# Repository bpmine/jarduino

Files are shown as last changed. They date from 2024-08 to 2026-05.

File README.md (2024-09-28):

# Jarduino

Le Jarduino est un ensemble de systèmes pour l'arrosage du jardin.

Il comporte les sous-ensembles suivants:
- Gestion des goutteurs
- Gestion des cuves
- Gestion des oyas

Le principal objectif du projet est de s'amuser tout en mettant à profit les compétences acquises lors d'une réponse à un cahier des charges pour un projet professionnel qui n'a finalement pas abouti.

La réalisation inclue des cartes électroniques conçues sur mesure, du logiciel, quelques petites pièces mécaniques et bien d'autres éléments....

## Illustrations (photos)

## Gestion des goutteurs

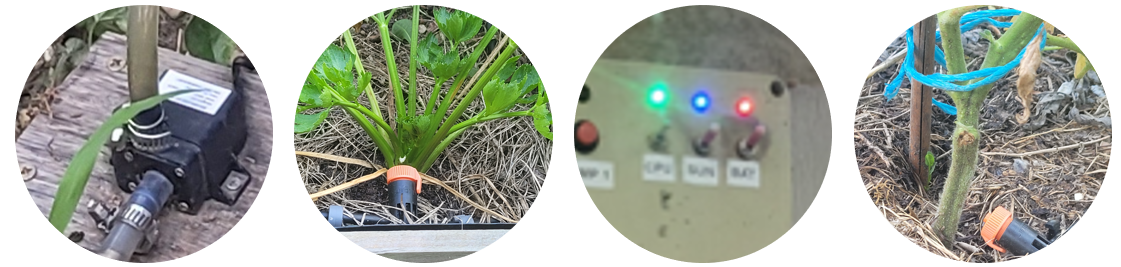
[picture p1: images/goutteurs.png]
Goutteurs


### Aux origines...

Le système de goutteurs est le "Jarduino" historique, mis en place assez rapidement (en 2019 ?) pour partir en vacances sans s'occuper de l'arrosage.

Il a fonctionné presque jusqu'au bout. Le panneau solaire s'est retourné (vent?), et sans énergie, il s'est arrêté...

Depuis 2019, chaque année, le Jarduino fonctionne toujours en se perfectionnant. Il a compté jusqu'à une cinquantaine de goutteurs en 2022.

### Jarduino 2

Ce Jarduino est un peu plus sérieux, basé sur de vraies cartes électroniques et non plus sur des platines de prototypage.

Il a été prévu en deux étapes:
- Tout d'abord une version simple basée sur un arduino Nano et une RTC;
- ensuite, une connexion Wifi via un ESP01 et la liaison série / modbus.

Il a fonctionné sans difficultés. Mais le module Wifi n'est toujours pas prêt (en 2024)...

#### Principe

Une cuve permet de stoker de l'eau. Un boîtier de contrôle alimenté par un panneau solaire avec une batterie pilote une pompe qui allimente les goutteurs.
Le boîtier pilote jusqu'à deux pompes et peut être programmé à une heure donnée pour une durée d'arrosage souhaitée.

Voir ici la description détaillée: [Système de goutteurs](./goutteurs)

## Gestion des cuves

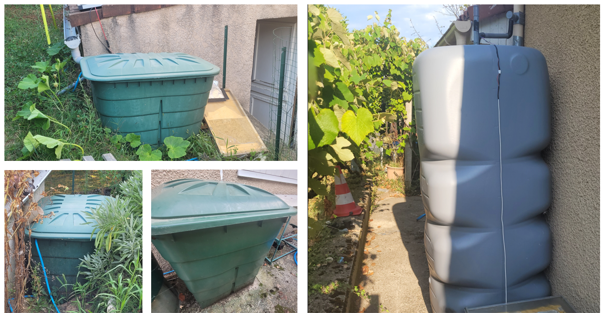
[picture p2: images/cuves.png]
Cuves


Plusieurs cuves récupèrent l'eau de pluie et permettent d'approvisioner les systèmes d'arrosage automatiques.
Un système de pompes contrôlables à distance permet de gérer leur niveau.

Voir ici la description détaillée: [Gestion des cuves](./cuves)

## Gestion des OYAs

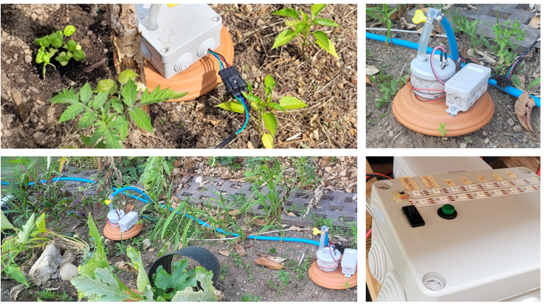
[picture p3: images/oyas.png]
Oyas


Le système permet de diffuser de l'eau aux plantes par la terre grâce à des sortes de petites jarres en argile appellées OYAs.
Ce dispositif a été déployé après les goutteurs, en 2023. Il remplace petit à petit le système de goutteurs.

Voir ici la description détaillée: [Gestion des OYAs](./oyas)

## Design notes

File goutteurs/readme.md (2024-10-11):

# Goutteurs (Jarduino2)

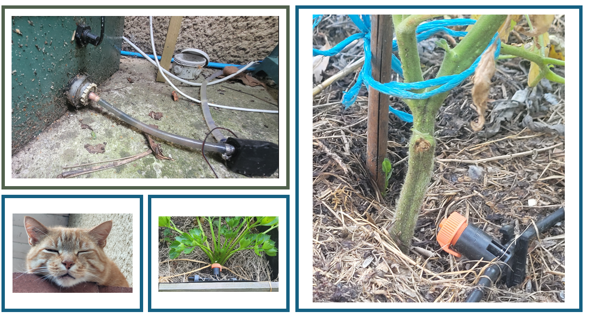
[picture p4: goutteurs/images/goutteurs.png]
Goutteurs


Jarduino2 est une évolution du premier jarduino fabriqué en 2019.

Le premier jarduino était construit avec des platines de prototypage et un arduino MKR Zero Wifi.

Ce nouveau jarduino est construit à partir d'un Nano. On peut le configurer à l'aide d'une interface MODBUS sur l'USB ou bien sur le port série d'extension.
Il est possible de lui ajouter une extension Wifi pour le relier au réseau.

## Vue d'ensemble

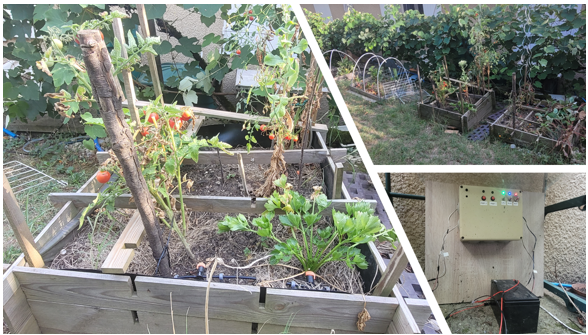
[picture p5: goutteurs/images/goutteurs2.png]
Goutteurs


Deux systèmes jarduinos étaient actifs en 2024, couvrant deux zones de jardin.
Chaque système est alimenté par une cuve à l'aide d'une pompe ou deux pompes.

Un coffret de commande permet de mettre ou non en service le système et de déclencher un arrosage en mode manuel.

Chaque coffret peut se programmer à l'aide d'un logiciel PC connecté à l'USB de la carte de commande. Cela permet d'activer ou non le mode automatique et de choisir l'heure de déclenchement et la durée d'arrosage.

Le coffret dispose de deux sorties pouvant commander deux pompes. Chaque voie peut alimenter jusqu'à 20 goutteurs. 

## Hardware

### Caractéristiques

  - Alimentation 12V;
  - Entrée de mesure de tension de panneau solaire;
  - 2 sorties 5W pour pompe (De type aquarium);
  - Sonde de température/Humidité;
  - LEDs et interrupteurs.

### Schéma

[Schéma de la carte de commande](./hard/jarduino2_nano/jarduino2_nano.pdf)

[Schéma de la carte d'interface à LEDs](./hard/jarduino2_ihm/jarduino2_ihm.pdf)

### PCBs

Chaque boîtier/coffret de commande est composé de deux circuits imprimés (PCBs):
- La carte de commande contient le microcontrôleur et gère tout le système
- la carte d'interface permet à l'utilisateur visualiser le fonctionnement et d'agir sur celui-ci.

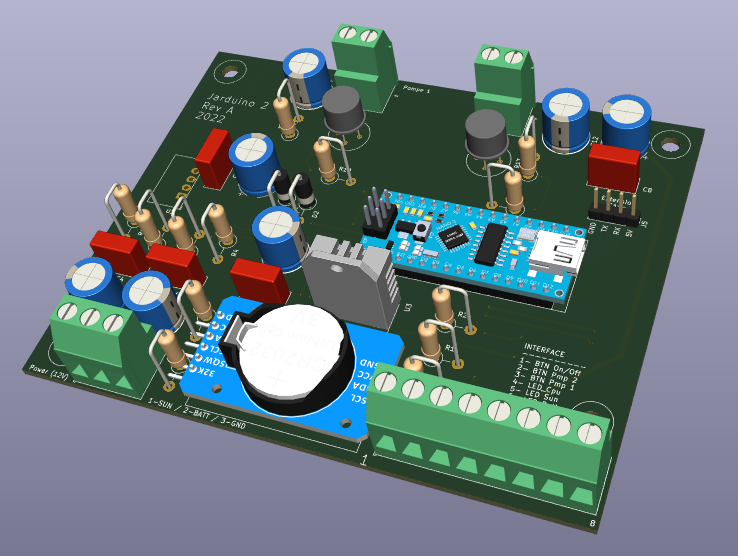
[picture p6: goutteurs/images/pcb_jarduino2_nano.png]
Carte de commande Jarduino2 Nano


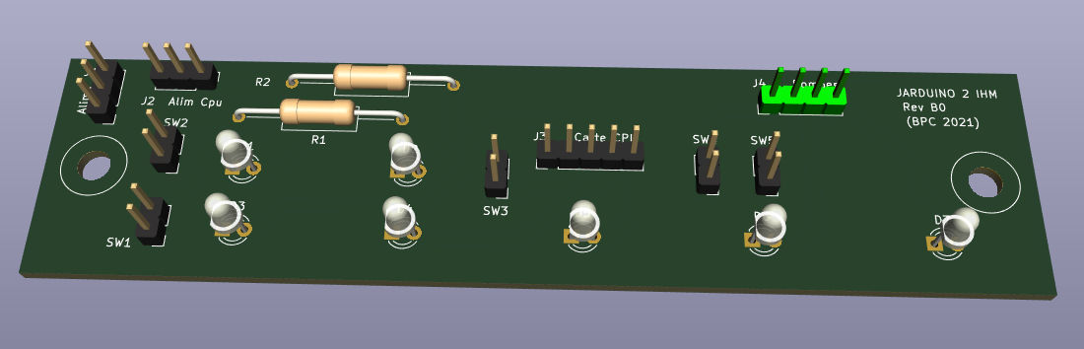
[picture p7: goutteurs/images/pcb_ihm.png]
Carte d'interface à LEDs


### Boîtier de commande

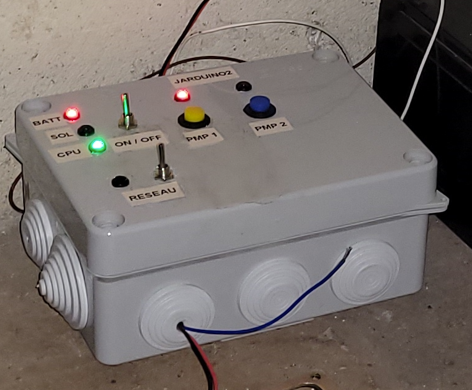
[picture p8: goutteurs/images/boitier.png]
Boîtier de commande Jarduino2


| LED | Description |
| --- | --- |
| BATT | Batterie OK |
| SUN | Panneau photovoltaique OK |
| Réseau | Réseau Wifi Activé |

NB: Il n'y a pas à ce jour (en 2024) de module Wifi terminé et apte à se connecter au réseau de domotique de la maison. C'est une fonction prévue à l'origine mais qui ne verra peut-être pas le jour puisque nous sommes en train de remplacer les goutteurs par des OYAs.

| Bouton | Type | Description |
| --- | --- | --- |
| ON/OFF | Inverseur  | Bouton de mise en service (Ne coupe pas l'alimentation mais fait passer le CPU en veille) |
| Réseau | Inverseur  | Bouton de mise sous tension de la carte Wifi (si présente) |
| Pump 1 | Poussoir  | Bouton de démarrage de l'arrosage manuel de la voie 1 |
| Pump 2 | Poussoir  | Bouton de démarrage de l'arrosage manuel de la voie 2 |

Le boîtier comporte les entrées/sorties suivantes:

| Voie | Type | Description |
| --- | --- | --- |
| Alimentation | Alim 12V  | Connexion d'une batterie extérieure (Plomb) |
| solaire | Alim 12V/20V | Connexion d'un panneau solaire pour recharger la batterie |
| Pompe 1 | Sortie 12V | Sortie de commande de la pompe 1 |
| Pompe 2 | Sortie 12V | Sortie de commande de la pompe 2 |

NB: Un module chargeur/régulateur solaire se trouve dans le boîtier pour permettre la charge de la batterie à l'aide du panneau solaire relié.

Ce système s'est avéré suffisant pour gérer le décalage entre les horaires à forte énergie solaire (jour) et la plage horaire idéale pour arroser (soirée/début de nuit).

## Logiciels

### Logiciel embarqué dans la carte de commande

[Logiciel gestion des goutteurs](./src)

### Logiciel PC pour configurer le système

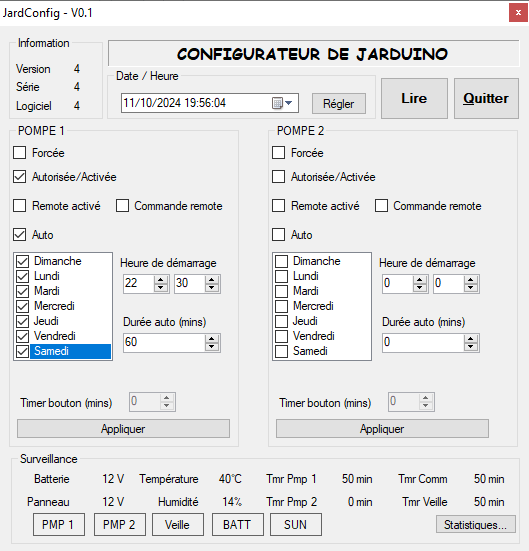
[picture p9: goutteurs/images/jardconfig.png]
Le logiciel JardConfig


Ce logiciel permet de configurer le boîtier Jarduino.
Pour cela, on branche un PC à l'USB de la carte de commande.

On peut:
- Régler l'heure

Et pour chaque voie (1 ou 2):
- Forcer la commande de la pompe
- Activer ou désactiver la pompe
- Activer et simuler le pilotage distant de la pompe
- Sélectionner le mode Auto (basé sur l'horloge)
- Régler l'heure d'arosage automatique
- Régler la durée de l'arrosage automatique
- Sélectionner les jours de semaine de l'arrosage automatique

Il permet également d'afficher l'état du système et quelques statistiques de fonctionnement.

Le logiciel communique avec le boîtier Jarduino à l'aide du protocole MODBUS (Voir ci-après).

## Protocole MODBUS

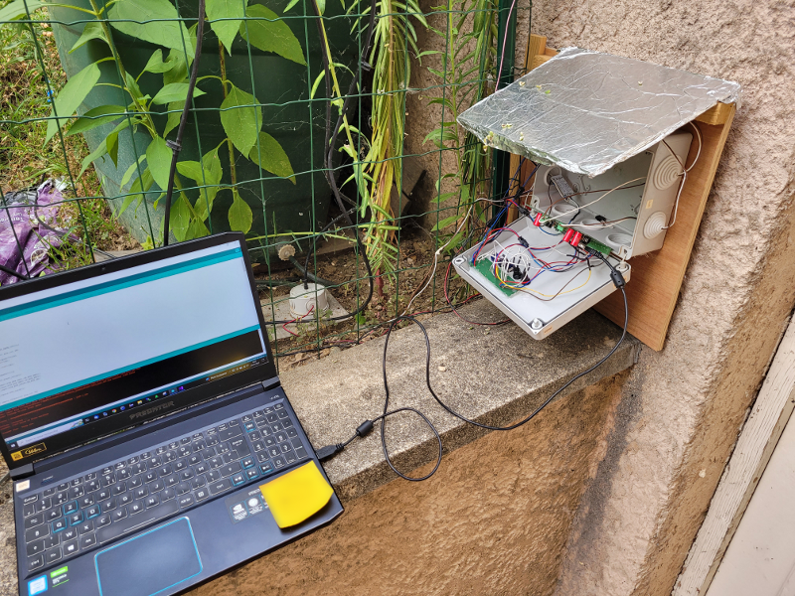
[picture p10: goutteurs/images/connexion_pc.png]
Connexion au PC


Le jarduino implémente un serveur/esclave MODBUS.

Seules les functions suivantes sont implémentées:

- 01 READ COIL STATUS
- 02 READ INPUT STATUS
- 03 READ HOLDING REGISTERS
- 04 READ INPUT REGISTERS
- 15 WRITE MULTIPLE COILS
- 16 WRITE MULTIPLE REGISTERS

### Table des COILs (Lecture/Ecriture)

Adresse | Description
--- | ---
10 | Forçage POMPE 1
11 | Autorisation/Activation POMPE 1
12 | Mode automatique POMPE 1
13 | Mode Distant POMPE 1
14 | Commande distante POMPE 1
--- | ---
20 | Forçage POMPE 2
21 | Autorisation/Activation POMPE 2
22 | Mode automatique POMPE 2
23 | Mode Distant POMPE 2
24 | Commande distante POMPE 2

Ces bits sont enregistrés en EEPROM sauf ceux qui correspondent au forçage des pompes et à leur commande distante.

NB: La commande à distance des pompe est appliquée seulement si le maître modbus communique toujours avec le jarduino nano.

### Table des Entrees (Lecture)

Adresse | Description
--- | ---
0 | Etat LED pompe 1
1 | Etat LED pompe 2
2 | Tension battery OK
3 | Tension panneau solaire OK
4 | Est en mode veille

### Table des INPUT REGISTERs (Lecture)

Adresse | Description
--- | ---
0 | Niveau de batterie en dxV
1 | Niveau du panneau solaire en dxV
2 | Temperature en °C
3 | Humidité en %
4 | Temps restant avant détection Comm perdue (en ms)
5 | Temps restant avant veille (en ms)
--- | ---
10 | Temps restant timer de pompe 1 (en min)
--- | ---
20 | Temps restant timer de pompe 2 (en min)
--- | ---
100 | Nombre total de boots
101 | Temps de fonctionnement total POMPE 1 (en H)
102 | Temps de fonctionnement total POMPE 1 (en H)
103 | Temps total d'ensoleillement (en H)
104 | Nombre total de pressions sur le bouton POMPE 1
104 | Nombre total de pressions sur le bouton POMPE 2
--- | ---
200 | Version (2 pour jarduino 2)
201 | Numéro de série du Jarduino
202 | Version du logiciel nano

### Table des HOLDING REGISTERs (Lecture/Ecriture)

Adresse | Description
--- | ---
0 | Année
1 | Mois
2 | Jour
3 | Heure
4 | Minute
5 | Seconde
--- | ---
10 | Heure de démarrage POMPE 1
11 | Minute de démarrage POMPE 1
12 | Durée (en min) d'activation de la POMPE 1
13 | Jours de la semaine pour l'activation de la POMPE 1 (Bit 0: Dimanche, Bit 1: Lundi, ..., Bit 7: Samedi)
14 | Réglage du délai du timer de pompe 1 (en min)
--- | ---
20 | Heure de démarrage POMPE 2
21 | Minute de démarrage POMPE 2
22 | Durée (en min) d'activation de la POMPE 2
23 | Jours de la semaine pour l'activation de la POMPE 2 (Bit 0: Dimanche, Bit 1: Lundi, ..., Bit 7: Samedi)
24 | Réglage du délai du timer de pompe 2 (en min)

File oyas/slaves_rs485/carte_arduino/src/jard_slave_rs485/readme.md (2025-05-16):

# Logiciel Esclave RS485 Oyas/Pompe

Ce logiciel pilote un noeud RS485 du système Oyas.
Logiciel compatible avec un module Arduino Nano.

## Protocole

Voir ../../../readme.md

## Taille du programme

| Description | Taille |
| --- | --- |
| Mémoire Flash | 11,154 kOctets |
| RAM | 485 Octets|

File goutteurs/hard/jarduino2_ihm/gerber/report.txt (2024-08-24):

Plot file "C:\DEV\GITHUB\modules_uino\jarduino2\schema\jarduino2\jarduino2_ihm\gerber\jarduino2_ihm-B_Cu.gbr" created.
Plot file "C:\DEV\GITHUB\modules_uino\jarduino2\schema\jarduino2\jarduino2_ihm\gerber\jarduino2_ihm-F_SilkS.gbr" created.
Plot file "C:\DEV\GITHUB\modules_uino\jarduino2\schema\jarduino2\jarduino2_ihm\gerber\jarduino2_ihm-B_Mask.gbr" created.
Plot file "C:\DEV\GITHUB\modules_uino\jarduino2\schema\jarduino2\jarduino2_ihm\gerber\jarduino2_ihm-Edge_Cuts.gbr" created.
Créer le fichier Gerber "job"  "C:\DEV\GITHUB\modules_uino\jarduino2\schema\jarduino2\jarduino2_ihm\gerber\jarduino2_ihm-job.gbrjob"

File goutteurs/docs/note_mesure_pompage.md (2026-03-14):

# Pompe jarduino historique (AD20P-1230A)

## Caractéristiques

| Caractéristique | Valeur |
|--|--|
| Tension | 12V cc |
| Courant | 400 mA |
| Puissance | 4.2 W |
| Débit maximum | 240 L/H |
| Hauteur maximum | 3 m |
| Pression | ? |
| Embouts | 8mm |

## Mesures

### Mesure jardin Paul (tuyau arrivee)

1L rempli en 02 mins 56 secs
20,5 L/H

~12 V

Environ 1m de dénivelé

### Mesure jardin côté réduit à bois (tuyau arrivee)

1L rempli en 7 mins 59 secs
8,57 L/H

Environ 1m50 de dénivelé

# Pompe AW500S

## Caractéristiques

| Caractéristique | Valeur |
|--|--|
| Tension | 12V cc |
| Courant | 920 mA |
| Puissance | 19 W |
| Débit maximum | 800 L/H |
| Hauteur maximum | 5 m |
| Pression | ? |
| Embouts | 20mm Vis mâle |

# Mesure 1
1L rempli en 14s
257L/H

12,7V
1,23A
15,5W

Conditions: Environ 1,5m de dénivelé

# Mesure 2
1,5L rempli en 37s
146L/Heure

Conditions: De la cuve principale vers celle du réduit via Wifi IO (et via EV ON)

# Pompe DP521

## Caractéristiques

Pompe à eau à membrane

| Caractéristique | Valeur |
|--|--|
| Tension | 12V cc |
| Courant | 2 A |
| Débit maximum | 3.5 L/H |
| Pression | 0.48 MPa |
| Embouts | 10 mm |

## Mesure de débit

Direct sur lavabo mais en passant par une EV

1,5 L rempli en 30S
Soit  3L/min (180 L/H)

A noter que la pompe fuit au niveau de ses vis si on bloque la sortie.

## Mesures électriques

Dispositif avec bidon lave glace modifié -> Filtre -> Pompe -> Débimètre -> EV

| Grandeur | Condition | Valeur |
| --- | --- | --- |
| Tension à la pompe | Avec de l'eau | 12,02 V |
| Courant dans la pompe | Avec de l'eau | 1,15 A |
| Puissance pompe | Avec de l'eau | 13,9 W |
| Tension à la pompe | Sans eau | 12,02 V |
| Courant dans la pompe | Sans eau | 0,66 A |
| Puissance pompe | Sans eau | 7,9 W |

Note: Le wattmètre consomme environ 1,24 W

Mesures complémentaires sur l'électrovanne:

| Grandeur | Condition | Valeur |
| --- | --- | --- |
| Tension EV | Pompe OFF | 12,20 V |
| Courant EV | Pompe OFF | 0,59 A |
| Puissance EV| Pompe OFF | 7 W |
| Tension EV | Pompe ON | 12,02 V |
| Courant EV | Pompe ON | 0,56 A |
| Puissance EV| Pompe ON | 6,7 W |

Note: Le wattmètre consomme environ 1,24 W

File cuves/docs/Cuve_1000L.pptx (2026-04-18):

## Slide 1

Mât avec capteurs de niveaux pour cuve 1000 L

2m

180cm
(Haut
cuve)

- Perçage
- Découpe à l'arrière pour visser le capteur
- Soudure arrière
- Eventuellement résine

140cm (Max)

90cm (Milieu)

Hauteur | Volume (L) | Volume (m³)
180 cm | 1000 | 1
140 cm | 778 | 0,778
90 cm | 500 | 0,500
20 cm | 111 | 0,111

20cm (Mini)

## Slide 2

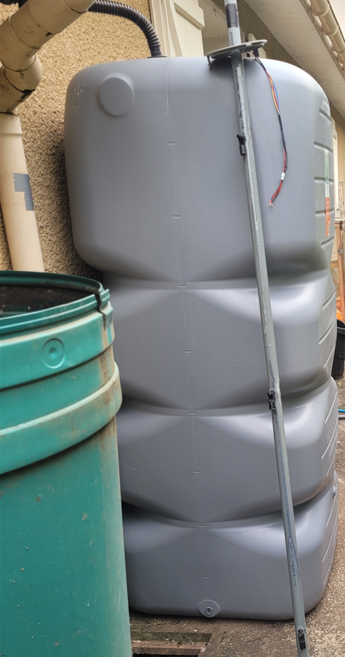
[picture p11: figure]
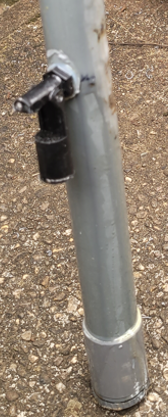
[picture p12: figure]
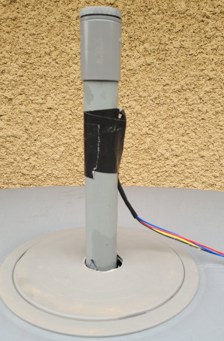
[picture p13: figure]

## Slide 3

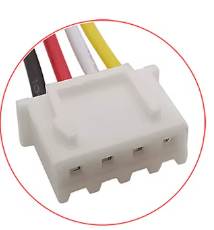
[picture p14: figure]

Bas

Milieu

Haut

Commun

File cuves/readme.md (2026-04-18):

# Cuves

Nous avons 4 cuves pour une capacité totale de 2200 L.

- Cuve principale de 1000 L
- cuve  "Paul" de 300 L
- cuve "Réduit" de 520 L
- cuve "Barbec" de 520 L

Deux cuves de 520 L et une de 300 L alimentent nos deux systèmes de remplissage automatique des OYAs.

Les cuves sont communicantes et un système permet de pomper l'eau de la cuve principale vers les autres. 

## Description des cuves

### Cuve principale (Main)

Cette cuve recueille l'eau du toit de la maison. D'une capacité de 1000 L, elle constitue la réserve principale.
Elle sert à alimenter la cuve "Paul" et aussi la cuve "Réduit" en cas de besoin.

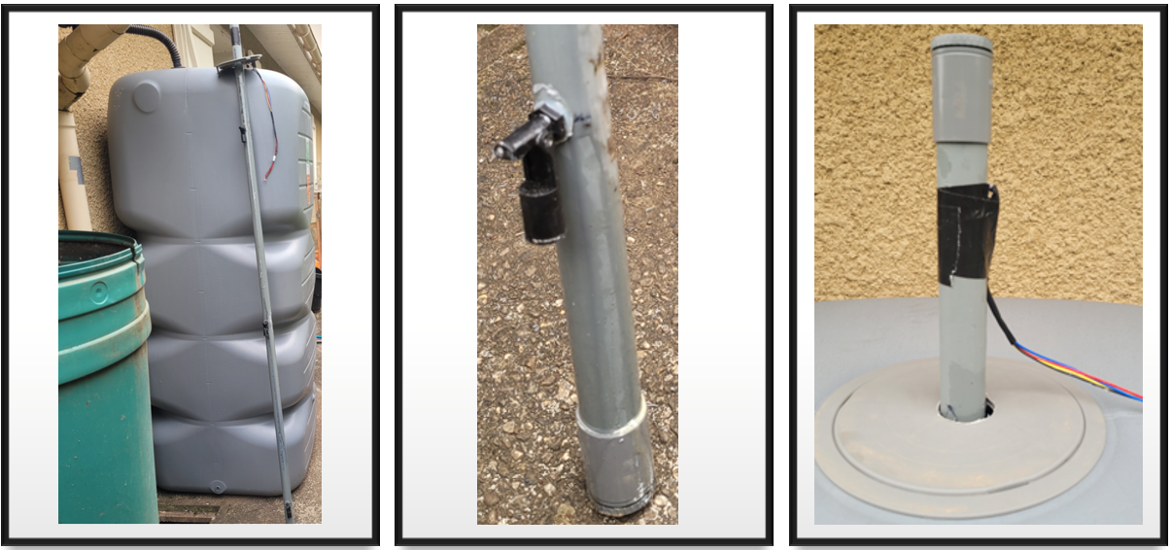
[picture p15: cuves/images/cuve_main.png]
Cuve principale 1000L


Comme on peut le voir sur la troisième photo, une colonne PVC de 32mm est utilisée comme jauge de niveau.
Cette solution permet d'éviter de percer des trous dans la paroi de la cuve (comme pour les autres).

Trois capteurs à flotteur sont fixés sur cette colonne qui ensuite est remplie de résine pour rendre le tout étanche et durable:

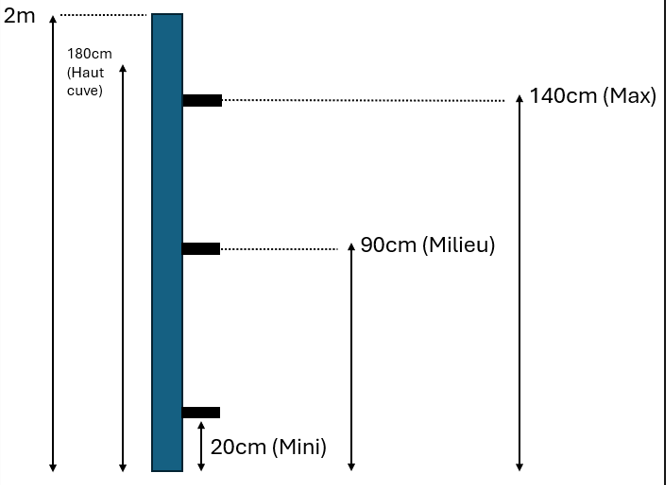
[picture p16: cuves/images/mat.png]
Mât de mesure


A la base de la cuve, un système de 2 pompes (précédées de filtres) permet de déplacer l'eau vers les autres cuves (Paul et Réduit):

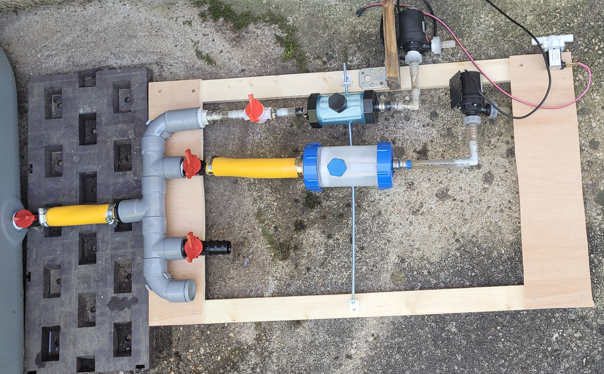
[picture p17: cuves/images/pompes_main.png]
Système de pompes


Le modèle de pompe utilisé est le AW500S 12V 5m 800L/H:

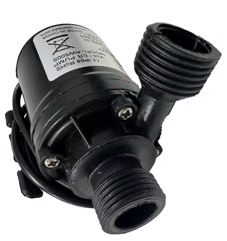
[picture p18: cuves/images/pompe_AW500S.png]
Pompe AW500S 12V 5m 800L/H


Pour la petite histoire, nous disposions avant 2023 à cet emplacement d'une cuve de moindre contenance.
Mal positionnée sur son support, un jour de pluie elle est tombée de tout son poids et BOOM !

Depuis, elle marche moins bien...

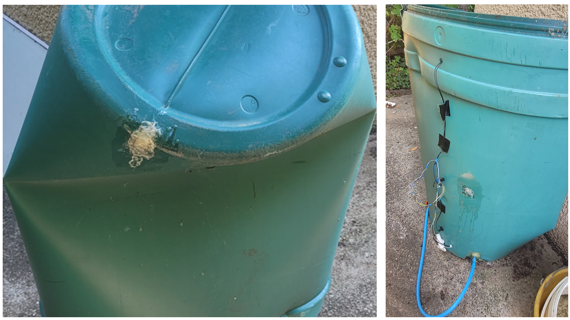
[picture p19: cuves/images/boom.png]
Cuve cassée


### Cuve Paul

La cuve "Paul" (de Paul) de 220 L permet d'alimenter un système de 6 oyas (en 2025). Anciennement, elle alimentait les derniers goutteurs pour des bacs de jardinage (5 bacs en 2024).

La détection de niveau est réalisée à l'aide de 3 capteurs avec flotteur montés sur la paroi de la cuve.

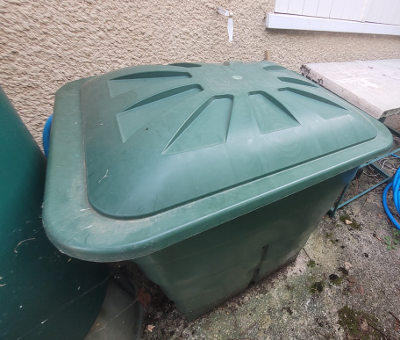
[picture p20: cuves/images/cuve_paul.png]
Cuve Réduit


### Cuve Réduit

Cette cuve de 520 L alimente un système de remplisage d'OYAs et permet également d'alimenter la cuve Barbecue si besoin.

La détection de niveau est réalisée à l'aide de 3 capteurs avec flotteur montés sur la paroi de la cuve. 

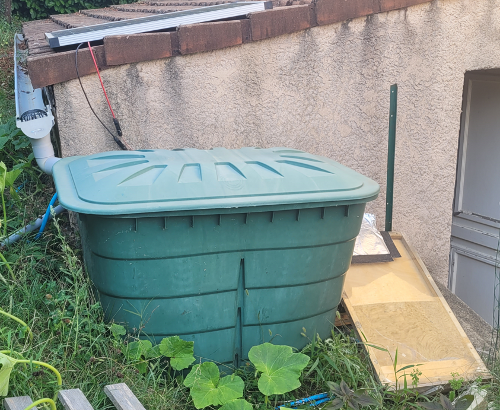
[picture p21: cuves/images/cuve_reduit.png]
Cuve Réduit


Le système de capteurs a montré ses limites car des fuites sont apparus au bout d'un an d'utilisation au niveau de ces capteurs.
Pour pallier au problème, de la résine a été utilisée pour recouvrir la zone sensible autour des capteurs.

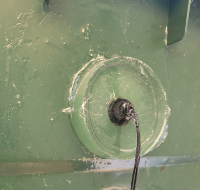
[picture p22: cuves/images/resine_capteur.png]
Résine sur les capteurs


### Cuve Barbecue

Cette cuve de 520 L alimente un système de remplisage d'OYAs et un système de goutteurs.
La détection de niveau est réalisée à l'aide de 3 capteurs avec flotteur montés sur la paroi de la cuve. 

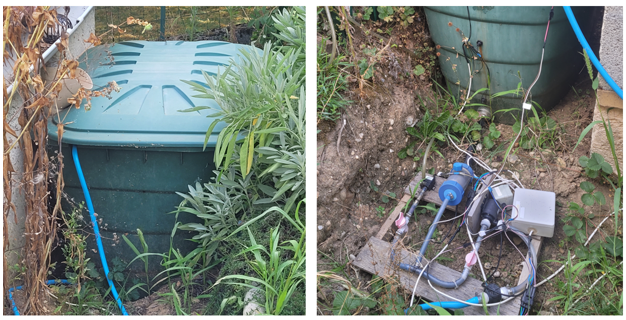
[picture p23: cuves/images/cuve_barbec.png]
Cuve Barbecue


## Filtres imprimés en 3D

Les électrovannes utilisées pour les OYAs et le transfert de l'eau inter-cuves, les pompes et les goutteurs requièrent une eau parfaitement filtrée.
Si pour les goutteurs d'entrée 8mm, cela paraît évident, il faut savoir que c'est également nécessaire pour les électrovannes. En effet, de petits morceaux d'algues peuvent bloquer une électrovanne en position ouverte.

C'est la raison pour laquelle des filtres ont été ajoutés à plusieurs endroits sur le tuyau (Cuves Paul, Réduit et Barbecue).

### Filtre sortie vers tuyau 4mm/8mm

Une pièce a été conçue et imprimée pour filtrer directement sur le tuyau PVC de sortie des cuves.
Elle a été utilisée avant 2023 lorsque tous les systèmes d'arrosages étaient en version goutteurs.

Ce filtre permet de brancher un tuyau 4 mm vers le système de gouteurs. 
Trop fragile, une version similaire avec une sortie 8 mm a ensuite été imprimée.

### Pré-filtre intérieur

Pour filtrer de plus gros morceaux avant le tuyau de sortie, la pièce suivante est vissée à l'intérieur des cuves (Réduit et Barbecue).

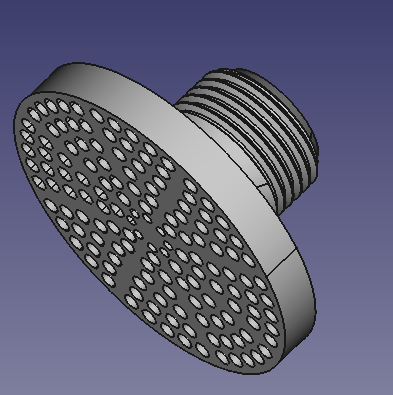
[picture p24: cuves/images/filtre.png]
Filtre intérieur


## Modules Wifi pour commander les pompes

### Description

Le module de pompage comporte:
- 1 alimentation 12V;
- 1 sortie pompe de 12V/5A;
- 3 entrées de type interrupteur (actif à l'état bas) pour la détection du niveau de cuve.

### Carte Wifi IO

Deux versions de cartes ont été réalisées:
- Carte wemos
- carte C3

La première à base d'un Wemos D1 mini (ESP8266). Cette carte fonctionne depuis 2024. Son boitier est petit et cela pose un problème avec la condensation. En 2025, deux cartes étaient déjà oxydées car elles baignaient dans l'eau. les boitiers ne sont pas parfaitement étanches.
Le projet se trouve ici: [Carte wemos](./carte_wemos)

La carte C3 est basée sur un module ESP32 C3 mini. Elle est censée mieux fonctionner... Fabriquée en 2026, elle est placée dans une boîte de dérivation plus grosse pour éviter que la condensation atteigne la carte.
Le projet se trouve ici: [Carte C3](./carte_c3)

La carte wemos s'avère plus puissante niveau Wifi et porte un peu plus loin. Les cartes C3 un peu moins bonnes et dépendantes de leur module C3 (dispertion).
Malgré tout, les cartes C3 semblent fonctionner correctement.

### Protocole d'échange avec MQTT

## Serveur de contrôle

Le serveur comporte un broker MQTT pour centraliser les connexions des différents modules du système.

Un serveur reddis stocke tous les états, les réglages et les commandes des différentes applications.

Les applications sont les suivantes:
- Interraction avec les modules de pompage
- Publication des états sur les écrans
- Webservice pour exposer les services à des clients
- Automatisme de contrôle
- Logger

## Module d'affichage

Le module d'affichage comporte un écran, OLED.

Il permet de visualiser l'état des cuves et l'activité de pompage en temps réel.

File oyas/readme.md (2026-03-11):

# Système de gestion des OYAs

## Présentation

Le but du système de remplissage automatique des OYAs est de pouvoir s'absenter pendant les vacances tout en laissant les OYAs se gérer tous seuls.

### Oyas

Les OYAs sont des sortes de pots en argile enterrés utilisés depuis des millénaires pour distribuer de l'eau à des cultures.

On remplit régulièrement ces pots. Grâce à leur porosité, l'eau se diffuse à travers l'OYAs au fur et à mesure où les racines des plantes assèchent la terre à proximité.

- Ils évitent les pertes d'eau par évaporation
- ne mouillent pas les feuilles des plantes
- ne mouille pas le sol en surface
- évitent le stress hydrique
- permettent de faire des économies d'eau

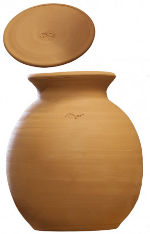
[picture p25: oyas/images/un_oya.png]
Un OYA


### Principe de fonctionnement

Des cuves récupèrent l'eau de pluie. A partir de ces cuves, un système comportant une pompe et plusieurs électrovannes permet de remplir les OYAs.

Le système rempli chaque OYA jusqu'au maximum ou bien selon le programme souhaité. La stratégie de remplissage est entièrement programmable.

## Description de nos réseaux d'OYAs

Notre installation comporte actuellement (en 2025) trois réseaux d'OYAs reliés chacun à une cuve et à son alimentation électrique autonome.

## Réseau A : Barbecue

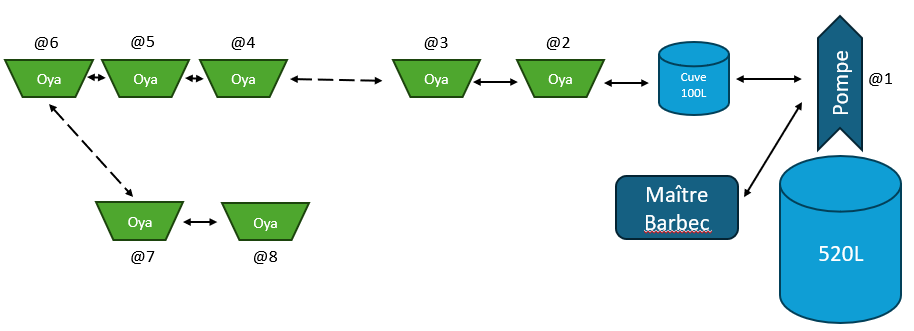
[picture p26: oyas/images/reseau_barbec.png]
Réseau Barbecue


C'est le plus ancien (mise en service en 2023). Il comporte à ce jour:

- 1 maître
- 1 pompe
- 7 OYAs
- 1 EV pour remplir un réservoir d'appoint

 Caractéristique | Description
-- | --
Nombre de nœuds | 10
Longueur | environ 30 m
Volume cuve | 520 L
Capacité totale des Oyas | 64 L (4x10 + 3x8 + cuve de 100L non gérée actuellement)
Alimentation | 1 Panneau solaire 120W + 2 Batteries 12V au plomb

La cuve et l'alimentation 12V déservent à la fois le système d'OYAs et un système de gestion de goutteurs alimenté par une petite pompe.

Ce réseau est à la fois composé de cartes électroniques  esclaves de "première génération" Rev Ax et de cartes récentes (Rev Gx produites en 2024).

Très bon retour sur le fonctionnement pendant l'été 2023. 
Excellent retour aussi en 2024.

A noter cependant la fragilité des électrovannes. Pour fonctionner correctement, il est nécessaire d'avoir une eau d'arrivée sans impureté. En effet, celle ci peut se déposer entre le corps et la membrane de l'électrovanne et bloquer cette dernière en position ouverte. Le tuyau 10mm transparent génère des algues qui sèchent pendant l'hiver lors de l'entreposage du système. Lors de la remise en service au printemps 2023, des morceaux d'algue de l'année précédente se sont détachées et sont venues perturber le fonctionnement des électrovannes.

## Réseau B : Réduit

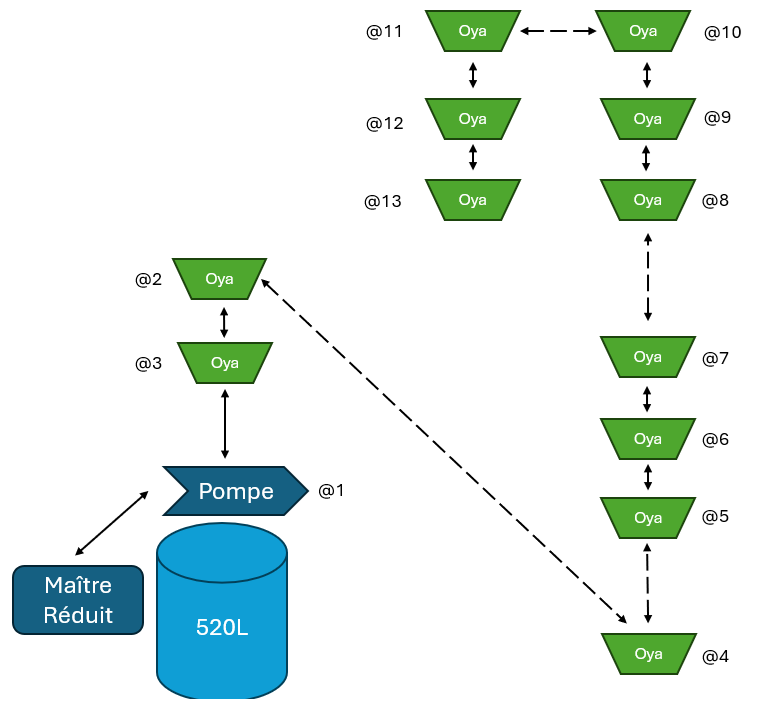
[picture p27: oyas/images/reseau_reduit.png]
Réseau Réduit


- 1 maître
- 1 pompe
- 12 OYAs (dont 4 ajoutés en 2025)

Caractéristique | Description
-- | --
Nombre de nœuds | 13
Longueur | environ 35 m
Volume cuve | 520 L
Capacité totale des Oyas | 100 L (2x10 + 10x8) 
Alimentation | 1 Panneau solaire 120W + 2 Batteries 12V au plomb

Mis en service en 2024. Etendu en 2025.

## Réseau C : Nord (Derrière la maison)

Réseau Nord

- 1 maître
- 1 pompe
- 6 OYAs

Caractéristique | Description
-- | --
Nombre de nœuds | 7
Longueur | environ 15 m
Volume cuve | 300 L
Capacité totale des Oyas | 48 L (6x8) 
Alimentation | ? (A définir)

Mis en service en 2025.

## Pilotage par Wifi

Les deux maîtres des OYAs sont accessibles par Wifi.

On peut prendre le contrôle et consulter en temps réel le niveau d'eau dans chaque OYA.
On peut également paramétrer le fonctionnement du système (heures et stratégies de remplissages, ...).

Ci-dessous une capture d'un monitoring du 14/08/2024:

Visualisation des niveaux

Durant nos vacances, les données sont également acheminées vers un cloud et mémorisées dans une base de données.
On peut ainsi voir évoluer les niveaux d'eau.

## Composants d'un réseau d'OYAs

### Réseau/Tuyau

Réseau RS485 et tuyau

Chaque système OYAs est composé d'un module maître et de plusieurs modules esclaves reliés entre eux par un réseau RS485 et un tuyau 12mm.

Le câble réseau comporte une alimentation 12V et les fils A et B du RS485.

Connecteur étanche

Le réseau possède deux résistances de terminaison de 120 Ohms aux deux extrémités. Il est également polarisé côté maître par une pull up et une pull down de 220 Ohms (Valeur encore susceptible de bouger).

Pour trouver les bonnes valeurs et étant donné la mauvaise qualité de câble utilisé, il faut effectuer des mesures de signal au bout du bus et vérifier que les tensions au repos de A et de B sont conformes à la norme RS485. 

Bouchon

__NB:__ Le dispositif de la photo ci-dessus contient une résistance de 128 Ohm. On appelle ça un "bouchon" !! (d'où le bouchon de liège...)

## Modules électronique de pilotage

### Module Pompe

Le module pompe contient une carte esclave RS485 en configuration "pompe".

Connecteurs:
- connecteur 4 voies bus RS485 + alim
- connecteur pompe
- connecteur débitmètre

Ce module est placé en sortie de cuve pour pomper l'eau et donner une certaine pression dans le tuyau. La pompe est nécessaire pour assurer un débit constant quelque soit le niveau d'eau dans la cuve et quelle que soit la hauteur relative entre la cuve et les différents OYAs.

Il faut aussi noter qu'une pression minimale est nécessaire pour ouvrir une électrovanne (voir ces caractéristiques).

Le schéma et le pcb de la carte sont ici: [Carte esclave RS485](./slaves_rs485/hard)

Plusieurs versions ont été réalisées, compatibles entre-elles. A ce jour le système est composé de façon hétérogène par ces différentes versions.

Version | Date | Description
-- | -- | --
Rev Ax | 2023 | Version initiale avec modules (forme en L)
Rev Bx | 2023 | Correction RX/TX inversé
Rev Dx | 2024 | Version sans module (tout intégré en CMS)
Rev Ex | 2024 | Avec modules (petite carte)
Rev Gx | 2024 | MAX485 en CMS (petite carte)

Le logiciel est ici: [Logiciel esclave RS485](.\slaves_rs485\src)

### Module Oya

Le module OYA contient une carte esclave RS485 en configuration "OYA".

Connecteurs:
- connecteur 4 voies bus RS485 + alim
- connecteur électrovanne
- connecteur niveaux

Il contient également une électrovanne 12V et un capteur de niveau.

Ce module est placé sur chaque OYA.

Module Oya Rev Bx (ouvert)

Le capteur de niveau comporte deux flotteurs qui ferment un contact en position basse.

Capteur de niveau

### Module Maître

Le maître des OYAs permet de commander une pompe et plusieurs électrovannes pour remplir des OYAs.

## Protocole réseau (RS485)

Le réseau est de type RS485. Il comporte un maître et plusieurs esclaves. Chaque esclave a une adresse unique (de 1 à 14 ou 1 à E en hexadécimal).

Seul le maître peut initier une communication. Un seul esclave peut répondre à une trame émise par le maître.

Types de messages du maître:

- Trame Commandes
- Trame Ping
- Trame Sync

Types de réponses d'un esclave:

- Trame Pompe
- Trame Oya
- Trame Pong

La communication se fait par cycles. Chaque cycle se termine par une trame Sync.

Durant un cycle, le maître envoie autant de trames __*"Commandes"*__ qu'il y'a d'esclaves configurés. Chaque trame __*"Commandes"*__ comporte un appel destiné à un esclave en particulier. Seul l'esclave appelé peut répondre avec l'une des deux trames __*"Oya"*__ ou __*"Pompe"*__.

Après un __*"Sync"*__, le maître doit impérativement attendre un temps minimum avant d'initier un nouveau cycle. Cela permet aux esclaves d'effectuer des traitements.

Pour plus de détails, voir

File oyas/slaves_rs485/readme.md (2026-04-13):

# Esclaves RS485

Ce sont des cartes esclaves permettant de piloter pompes et oyas.

## Types de carte

### Carte_arduino

Design initial à base de modules arduino nano.
Gestion des pompes et des oyas avec la même carte.
Les premières cartes comportaient un module RS485 indépendant. Il a ensuite été intégré sur la carte mère.
Ces cartes sont alimentées par le régulateur du module nano.
Il y'a eu plusieurs versions de cette "première" carte. 

Cette carte existe depuis 2023. Elle a donc déjà un long historique. Elle fonctionnait avec un vieux protocole qui a été remplacé dans la dernière version de logiciel.

### Carte AT328

Seule l'alimentation à découpage provient d'un module extérieur. Tout le reste a été intégré en composant CMS ou tranversants (connecteurs).
Il n'y a plus de capteur de température DHT22.
Il n'y a qu'un seul gros bornier pour accueillir les fils du bus.
Elle peut gérer soit une pompe, soir un oya.
Le logiciel utilise le arduinocore (compatible arduino).

### Carte MSP430

Même principe que la carte à base de AT328 mais ne peut gérer qu'un oya.
Il était prévu de pouvoir à terme gérer également la pompe avec cette carte.

Mais 2 MSP430 sur 3 achetés sur aliexpress s'avèrent impossible à programmer! Il semblent qu'il aient été bloqués par logiciels. Peut-être le vendeur a-t-il mélangé des MSP430 corrects aau milieu d'une série bloquée? 

Le choix s'expliquait par ma connaissance de ce micro suite à son utilisation dans l'un de mes projets profesionnels dans les années 2000. 

Même si j'adore ce micro, ce n'était pas une bonne idée:
- L'environnement IAR gratuit n'est plus dispo en téléchargement pour <32k
- Le MSP430F1232 est devenu obsolète

### Carte M0 (avec ATSAMD21G18A-A)

Suite aux problèmes rencontrés par les MSP430 achetés sur aliexpress, je décide d'abandonner définitivement le MSP430.

Je change également de critère pour choisir le cpu:
- Avoir une clock interne performante et assez précise pour ne pas nécessiter de quartz
- Compatible avec l'un des environnements que je connais
- Suffisament de périphériques et de broches pour pouvoir l'utiliser sur d'autres projets
- ...

Tant pis si je sors de l'Arduino... retour aux sources !

Le choix est le ATSAMD21G18A. La soudure à la main est assez délicate mais j'y arrive.

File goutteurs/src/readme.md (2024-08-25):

# Sources pour la gestion des goutteurs

Le logiciel embarqué dans le jarduino est ici: [Logiciel jarduino](./jard_nano)

Le logiciel PC qui permet de configurer un jarduino est ici: [Logiciel PC](./JardConfig_PC)

Logiciel pour la carte wifi (en cours de développement): [jard_wifi](./jard_wifi)

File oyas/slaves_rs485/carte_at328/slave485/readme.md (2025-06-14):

# Logiciel Esclave RS485 Oyas/Pompe

Ce logiciel pilote un noeud RS485 du système Oyas.

Fuse:
Extended: FD
High: 0xD2
Low: 0xFF

## Protocole

### Principe

Le maître envoi une requête à un esclave et attend une réponse de celui-ci.

Il existe une adresse de broadcast permettant de maintenir la communication réseau vivante pour tous les esclaves qui peuvent considérer alors le réseau comme sain et maintenir les commandes en cours.
Aucun esclave n'est autorisé de répondre à cette adresse de broadcast.

Il utilise des fonctions pour agir sur un esclave. A chaque fonction correspond un format de réponse associé.

### Format de la trame

#### Requête

Seul le maître peut envoyer une requête.

[SOH] {Adresse esclave} {Fonction} {datas} {Checksum} [STX]

Elément | Description | exemple(s)
--- | --- | ---
[SOH] | Valeur 1 (Voir table ASCII) | 
{Adresse esclave} | Caractère de 'A' à 'Y' identifiant un noeud/esclave (1 caractère) | 'A': Pompe, 'B': Oya 1, ...
{Fonction} | Fonction à executer sur le noeud (1 caractère) | '1': Commander la pompe, '2': Commander l'électrovanne, 'p': Ping, ...
{datas} | Donnée pour la commande (1 octet codé en chaîne hexadécimale) |  '12' = 18 , 'AE' = 174, '01' = 1, ...
{Checksum} | Somme de contrôle (1 octet codé en chaîne hxadécimale) | 'AE' = 174, ...
[STX] | Valeur 2 (Voir table ASCII) |

Nota: L'adresse 'Z' est une adresse spéciale qui ne doit jamais être utilisée sur un réseau. C'est l'adresse initiale du noeud après une programmation du micro avec le #define FORCE_INIT. Toujours revenir à un programme sans ce #define après réinit.

Le checksum correspond à la somme modulo 256 de tous les octets envoyée en commençant après le SOH jusqu'aux datas incluses.

### Liste des fonctions

Fonction | Description | Paramètre | Retour | exemple
--- | --- | --- | --- | ---
'1' | Actionner une pompe | 1= ON, 0= OFF | [SOH]{addr}1{Status}{Temp}{Hum>]{Cs>][STX] | [SOH]A100[<Cs>][STX] => OFF, [SOH]A101[<Cs>][STX] => ON
'2' | Actionner une électrovanne | 1= ON, 0= OFF | [SOH]{addr}1{Status}{Temp}{Hum}{Cs}[STX] | [SOH]B200{Cs}[STX] => OFF, [SOH]B201{Cs}[STX] => ON
'@' | Changer l'adresse du noeud | code ascii de la nouvelle adresse (codé en chaîne hexa) | [SOH]{nouvelle addr}@{Status}{Nouvelle addr}{Cs}[STX] | [SOH]Z@59{Cs}[STX] => Le noeud 'Z' devient 'Y' (Ascii 89 / 59H)
'f' | Changer la fonction principale du noeud | code ascii de la nouvelle fonction (codé en chaîne hexa) | | [SOH]Zf31{Cs}[STX] => Le noeud 'A' devient une pompe '1'
'e' | Activer ou non le noeud (un noeud désactivé ne commandera pas sa pompe ou son électrovanne) | "01" pour activer ou "00" pour désactiver | | [SOH]Ae01{Cs}[STX] => Le noeud 'A' est activé
's' | Retourne le temps en s d'actionnement de la pompe ou de l'électrovanne | Laisser à "00"  | | [SOH]As00{Cs}[STX]
'S' | Remet à zéro le compteur de temps | Laisser à "00" | | [SOH]AS00{Cs}[STX]
'r' | Retourne les compteurs d'erreur réseau du noeud| Laisser à "00" | | [SOH]Ar00{Cs}[STX]
'R' | Remet à zéro les compteurs d'erreurs | Laisser à "00" | | [SOH]AR00{Cs}[STX]
'p' | Ping | Valeur quelconque entre '00' et 'FF' | Echo de la valeur passée en paramètre | [SOH]Ap09{Cs}[STX] -> Réponse: [SOH]Ap09{Cs}[STX]

## Taille du programme

| Description | Taille |
| --- | --- |
| Mémoire Flash | 11,154 kOctets |
| RAM | 485 Octets|

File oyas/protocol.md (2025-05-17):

# Protocole

Ce protocole est commun à toutes les cartes esclaves.
Le réseau comporte un maître et plusieurs esclaves. 

## Couche physique

Il est basé sur du RS485 à 9600 bauds sans parité.

Le maître comporte une terminaison de 120 Ohms et 2 résistances de polarisation de A/B.

## Adressage

Une adresse comprise entre 1 et 14 est affectée à chaque esclave. Chaque adresse doit être unique sur son réseau.

Salon la version de la carte, cette adresse est soit configurable à l'aide d'un switch rotatif à 16 positions, soit mémorisée dans l'EEPROM du micro.

Les positions 0 et 15 sont réservées:
- 0: Désactiver l'esclave (il ne répond plus);
- 15: Prendre la valeur d'adresse configurée en EEPROM.

Pour les modèles sans commutateur, il faut écrire la valeur en EEPROM (Voir les #define du programme associé pour injecter un programme de configuration).

L'adresse 1 est exclusivement réservée à la pompe et il ne peut y avoir qu'une seule pompe sur un réseau.

Le maître n'a pas d'adresse.

## Principe

Seul le maître peut initier une communication. Un seul esclave peut répondre à une trame émise par le maître.

Types de messages du maître:

- Trame Commandes
- Trame Ping
- Trame Sync
- Trame de Raz du temps de fonctionnement
- Trame de Raz du nombre d'erreurs

Types de réponses d'un esclave:

- Trame Pompe
- Trame Oya
- Trame Pong

La communication se fait par cycles. Chaque cycle se termine par une trame Sync.

Durant un cycle, le maître envoie autant de trames __*"Commandes"*__ qu'il y'a d'esclaves configurés. Chaque trame __*"Commandes"*__ comporte un appel destiné à un esclave en particulier. Seul l'esclave appelé peut répondre avec l'une des deux trames __*"Oya"*__ ou __*"Pompe"*__.

Après un __*"Sync"*__, le maître doit impérativement attendre un temps minimum avant d'initier un nouveau cycle. Cela permet aux esclaves d'effectuer des traitements.
Cette technique permet d'éviter qu'une éventuelle surcharge de cpu d'un esclave ne vienne perturber le cycle réseau.

Certaines trames du maître ne doivent pas induire de réponse (Trames Raz et Sync par exemple).

### Format d'une trame

Toute trame doit avoir le format suivant:

Trame

Elément | Taille | Description | exemple(s)
--- | --- | --- | ---
SOH | 1 | Valeur 1 (Voir table ASCII) | 
LEN | 2 | Taille de la trame comprenant Length + ID msg + datas + Checksum (1 octet codé en chaîne hexadécimale) | '09' = 9 octets
ID | 1 | Identifiant (ou type) de trame(1 caractère) | 'm' = Trame de commande du maître, 'o' = Réponse d'un oya...
DATA | n=2p | Données propres au type de trame (n octets codés en chaîne hexadécimale) |  Voir chaque type de trame
CS | 2 | Somme de contrôle (1 octet codé en chaîne hexadécimale) | 'AE' = 174
STX | 1 | Valeur 2 (Voir table ASCII) |

Chaque chaine hexadécimale est codée selon la logique du MSB first. C'est à dire que l'on envoi l'octet de poids fort en premier.
Exemple le mot 16 bits 0xABCD sera transcrit 'ABCD' dans la trame

### Liste des types de trames

ID | Maître | Esclave | Description
--- | --- | --- | ---
m | X | | Trame de commande générale envoyée par le maître
p | | X | Trame de réponse envoyée par un esclave de type pompe lorsque son adresse est contenue dans la trame de commande générale
o | | X | Trame de réponse pour un oya (même principe que pour la trame p)
S | X | | Trame SYNC de synchronisation fin de cycle
i | X | | Trame PING envoyé par le maître pour tester un esclave en particulier
y | | X | Trame PONG de réponse d'un esclave à un PING
t | X | | Trame de RAZ du temps destinée à un esclave
z | X | | Trame de RAZ du nombre d'erreurs destinée à un esclave

### Description détaillée des types de trames

#### Principes communs à toutes les trames

#### Trame de commande générale (m)

[SOH]09m{Commandes}{Adresse}{Checksum}[STX]

Elément | Description | exemple(s)
--- | --- | ---
Commandes | 16 bits B15..B0 codés en chaîne hexadécimale | '0802' = Pompe (@1) et oya (@11) actifs
Adresse| Adresse du noeud concerné par la réponse | '0E' = esclave 14, '01' = pompe, ...

B1 correspond à la pompe (activée si à 1)
B2..B14 correspondent aux Oyas @2 à @14 (activés si à 1)

NB: B0 et B15 sont réservés et aucun esclave ne doit interpréter ces commandes.

Les adresses sont comprises entre 1 et 14. Aucun esclave ne doit répondre à des sollicitations pour les adresses en dehors de cet intervalle.

Lorsque le maître envoi cette trame, il attend une réponse de la part de l'esclave concerné. En cas d'absence de réponse de l'esclave, celui-ci est considéré comme non connecté.

#### Trames de réponse d'un esclave (p,o)

Les trames de réponse d'un Oya et d'une pompe sont très similaires.
La différence réside dans l'interprétation de l'octet de statut et par la présence du débit pour la pompe.

[SOH]XXp{Statut}{tick}{temp}{hum}{volt}{total time}{total errs}{flow}{Checksum}[STX]

Elément | Description | exemple(s)
--- | --- | ---
Statut | 1 octet de statut B7..B0 codés en chaîne hexadécimale | '02' = 
tick |  | 

### Description détaillée des échanges

#### Echange Commande/Réponse

#### Echange Ping/Pong

### Description d'un cycle

#define STATUS_CMD     		(0x01)
#define STATUS_ON     		(0x02)
#define STATUS_LVL_LOW    	(0x04)
#define STATUS_LVL_HIGH   	(0x08)

#define ADDR_SYNC		'S'		///< Synchro fin de cycle (pour laisser du temps aux esclave de faire leur traitement)

#### Timing notable

Temps de cycle
Temps entre le sync et un nouveau cycle

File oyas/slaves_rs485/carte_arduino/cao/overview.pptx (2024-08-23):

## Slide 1


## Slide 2

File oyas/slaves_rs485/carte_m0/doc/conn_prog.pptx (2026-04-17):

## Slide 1


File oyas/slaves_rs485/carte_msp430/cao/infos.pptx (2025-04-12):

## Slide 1


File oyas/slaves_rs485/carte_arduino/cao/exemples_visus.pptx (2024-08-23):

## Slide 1

Cartes esclave 2023


Cartes esclave 2024

- Rev Ax: Carte en L avec modules
- Rev Bx: Correction inv Rx/Tx
- Rev Cx: Non existante


- Rev Dx: Mini carte en CMS avec ATMEGA328P


- Rev Ex: Mini carte avec modules + CMS
- Rev Fx: Non existante (Correction inv Rx/Tx + piste LED)
- Rev Gx: Remplacement module RS485 par MAX485E CMS

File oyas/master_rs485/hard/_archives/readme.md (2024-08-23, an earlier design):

# Archives des cartes Master RS485

Ce dossier contient les vieux designs (pour la maintenance des cartes encore en service)...

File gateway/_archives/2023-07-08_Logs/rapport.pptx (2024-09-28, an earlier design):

## Usage OYAS vacances 2023

Début: 17/07/2023 à 16:38
Fin: 05/08/2023 à 22:00 (soit 19 Jours)
Consommation: 1.244 Ah (soit 65 mAh par jour en moyenne)
Remplissages:
- Lundi 17/07/2023 (manu)
- Mardi 18/07/2023 (manu)
- 21/07/2023
- 25/07/2023
- 28/07/2023
- 01/08/2023
- 04/08/2023
- 05/08/2023 (manu)

Configuration:
- 5 Oyas / 1 pompe
- Algo type "round robin"
- Temps maxi par oya: 1 min
- Temps maxi total: 5 mins

Volume oyas:
- a,b,c,d,f de xL environ (grand)
- e de yL environ (petit)

Bugs/Améliorations:
- Augmenter le temps d'action de 5 à 10 mins
- Remplacer les , par des ; dans les logs
- Logguer les temp et hum par oya plutôt que des stats

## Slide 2


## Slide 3


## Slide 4


Oya | Temps cumulé de remplissage
B | 519 s
C | 393 s
D | 310 s
E | 201 s
F | 361 s

Temps total de remplissage: 1784 s (soit presque 30mins)

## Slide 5

Opérations de remplissage

________________________________________
OYA d:
2023-07-17 22:08:33> durée: 0:00:06 (Niveau final=100%)
2023-07-18 10:05:46> durée: 0:00:12 (Niveau final=100%)
2023-07-21 12:02:25> durée: 0:00:55 (Niveau final=100%)
2023-07-25 12:02:19> durée: 0:00:26 (Niveau final=50%)
2023-07-28 12:02:22> durée: 0:01:00 (Niveau final=50%)
2023-08-01 12:02:21> durée: 0:01:03 (Niveau final=50%)
2023-08-04 12:02:22> durée: 0:01:00 (Niveau final=50%)
2023-08-05 21:56:46> durée: 0:00:28 (Niveau final=100%)
________________________________________
OYA e:
2023-07-17 18:30:22> durée: 0:00:06 (Niveau final=100%)
2023-07-18 10:05:58> durée: 0:00:05 (Niveau final=100%)
2023-07-21 12:03:20> durée: 0:00:39 (Niveau final=100%)
2023-07-25 12:02:45> durée: 0:00:48 (Niveau final=100%)
2023-07-28 12:03:22> durée: 0:00:39 (Niveau final=100%)
2023-08-01 12:03:24> durée: 0:00:47 (Niveau final=100%)
2023-08-05 21:57:14> durée: 0:00:17 (Niveau final=100%)
________________________________________
OYA f:
2023-07-17 17:05:22> durée: 0:00:06 (Niveau final=100%)
2023-07-17 22:08:39> durée: 0:00:10 (Niveau final=100%)
2023-07-18 10:06:03> durée: 0:00:16 (Niveau final=100%)
2023-07-21 12:03:59> durée: 0:01:01 (Niveau final=50%)
2023-07-25 12:03:33> durée: 0:01:01 (Niveau final=50%)
2023-07-28 12:04:01> durée: 0:00:59 (Niveau final=50%)
2023-08-01 12:04:11> durée: 0:00:11 (Niveau final=0%)
2023-08-04 12:03:22> durée: 0:01:05 (Niveau final=50%)
2023-08-05 21:57:31> durée: 0:01:01 (Niveau final=50%)
2023-08-05 21:59:01> durée: 0:00:11 (Niveau final=100%)

________________________________________
OYA b:
2023-07-17 18:30:16> durée: 0:00:06 (Niveau final=100%)
2023-07-17 22:08:21> durée: 0:00:06 (Niveau final=100%)
2023-07-18 10:05:24> durée: 0:00:12 (Niveau final=100%)
2023-07-21 12:00:21> durée: 0:00:59 (Niveau final=50%)
2023-07-25 12:00:18> durée: 0:01:00 (Niveau final=50%)
2023-07-25 12:04:34> durée: 0:00:05 (Niveau final=50%)
2023-07-28 12:00:18> durée: 0:00:58 (Niveau final=50%)
2023-08-01 12:00:23> durée: 0:01:00 (Niveau final=50%)
2023-08-01 12:04:22> durée: 0:00:15 (Niveau final=100%)
2023-08-04 12:00:19> durée: 0:00:59 (Niveau final=50%)
2023-08-04 12:04:27> durée: 0:00:11 (Niveau final=100%)
2023-08-05 21:53:23> durée: 0:02:26 (Niveau final=50%)
2023-08-05 21:55:55> durée: 0:00:22 (Niveau final=100%)
________________________________________
OYA c:
2023-07-17 22:08:27> durée: 0:00:06 (Niveau final=100%)
2023-07-18 10:05:36> durée: 0:00:10 (Niveau final=100%)
2023-07-21 12:01:20> durée: 0:01:05 (Niveau final=50%)
2023-07-25 12:01:18> durée: 0:01:01 (Niveau final=50%)
2023-07-28 12:01:16> durée: 0:01:06 (Niveau final=50%)
2023-08-01 12:01:23> durée: 0:00:58 (Niveau final=50%)
2023-08-01 12:04:37> durée: 0:00:23 (Niveau final=100%)
2023-08-04 12:01:18> durée: 0:01:04 (Niveau final=50%)
2023-08-04 12:04:38> durée: 0:00:11 (Niveau final=100%)
2023-08-05 21:56:17> durée: 0:00:29 (Niveau final=100%)

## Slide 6


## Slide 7


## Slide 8


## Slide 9


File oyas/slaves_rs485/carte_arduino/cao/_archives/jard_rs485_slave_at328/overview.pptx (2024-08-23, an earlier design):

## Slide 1


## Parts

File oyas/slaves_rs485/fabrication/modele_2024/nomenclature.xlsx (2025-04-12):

Description | PU | Qté | Total | Lien achat
Composants électroniques | 44.61 | 1 | 44.61
PCB | 5.52 | 1 | 5.52
Oya |  | 1 | 0 | Botanic
Couvercle / soucoupe 17mm | 2.9 | 1 | 2.9 | Castorama
Capteur de niveau - Modèle 200mm | 7.19 | 1 | 7.19 | https://fr.aliexpress.com/item/4000467977004.html
Electrovanne 12V diam. 12mm | 6.13 | 1 | 6.13 | https://fr.aliexpress.com/item/4000185704146.html
Boîte de dérivation ronde | 2 | 1 | 2 | Castorama
Boîte de dérivation rectangulaire | 2 | 1 | 2 | Castorama
Cosse 6.3mm | 0.088 | 2 | 0.176 | https://fr.aliexpress.com/item/1005007995094485.html
Ecrous M4 | 0.2 | 4 | 0.8
Rondelles M4 | 0.04 | 2 | 0.08
Vis M4 | 0.2 | 2 | 0.4
Embout tuyau 10mm sur 6cm | 0.14 | 2 | 0.28
Collier 10mm - 16mm | 0.238 | 2 | 0.476 | https://fr.aliexpress.com/item/1005004790494883.html
Coude 10mm / 12mm | 0.292 | 1 | 0.292
Couple de connecteurs étanche bus (4 voies) | 1.83 | 1 | 1.83 | https://fr.aliexpress.com/item/4000029686070.html
 |  | Total | 74.684

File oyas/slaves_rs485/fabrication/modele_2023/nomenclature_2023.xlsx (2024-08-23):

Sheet: Ensemble
Module esclave
Description | PU | Qté | Tot TTC | Farnel | Lien ALI
Carte CI + composants | 25.817 | 1 | 25.817
Electrovanne 12V | 4.64 | 1 | 4.64 |  | https://fr.aliexpress.com/item/4000185704146.html?mp=1
Capteur de niveau d'eau | 6.24 | 1 | 6.24 |  | https://fr.aliexpress.com/item/1005001431651257.html?curPageLogUid=VyN6FfBQ6zCj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
Fils | 0.97 | 0.2 | 0.194
Cosses | 0.0352 | 2 | 0.0704
Boîte de dérivation | 2.5 | 1 | 2.5
Raccord T 12mm | 1.953333333 | 1 | 1.953333333
Racord coude 12mm et 10mm | 0.292 | 1 | 0.292
Tuyau 10 mm (en m) | 2.18 | 0.14 | 0.3052 |  | Casto
Colliers 10mm | 0.292 | 2 | 0.584
Colliers 12mm | 0.274 | 1 | 0.274
Dessous de vase | 2.85 | 1 | 2.85
Boulons tête fraisée | 0.2 | 4 | 0.8
Ecrous | 0.2 | 4 | 0.8
Rondelles | 0.04 | 4 | 0.16
Couple connecteur étanche bus | 1.16 | 2 | 2.32
 |  |  | 0
 |  |  | 0
 |  |  | 0
 |  | Total | 49.79993333
Module maître | PU | Qté | Tot TTC |  | Lien ALI
ESP | 12
Module RS485
 |  | 74.98
 |  | 6.248333333

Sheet: Carte Mods
Module esclave
Description | PU | Qté | Tot TTC | Farnel | Lien ALI
Nano 168P | 2.91 | 1 | 2.91
Module RS485 | 0.7 | 1 | 0.7
Bornier 4 contacts à vis | 0.64 | 2 | 1.28
Bornier 2 contacts à vis | 0.534 | 1 | 0.534
Bornier 3 contacts à vis | 0.588 | 1 | 0.588 |  | https://fr.aliexpress.com/item/1005001677869988.html
Résistances 100k | 0.03 | 7 | 0.21
Résistance 150 | 0.03 | 2 | 0.06
Résistance 50 | 0.2 | 1 | 0.2
Capa 20µF | 1 | 1 | 1
Capa 10µF | 0.5 | 1 | 0.5
Capa 10nF | 0.5 | 1 | 0.5
Capa 100nF | 0.5 | 2 | 1
Diode de redressement | 0.5 | 1 | 0.5
Transistor 2N2222 | 1.52 | 1 | 1.52
Diode de protection | 0.5 | 3 | 1.5
Transistor P03P4L-04 | 1.449 | 1 | 1.449 |  | https://fr.aliexpress.com/item/1005002656127438.html?curPageLogUid=4WkS0xZRCrQT
Résistance 40k | 0.03 | 1 | 0.03
Résistance 10k | 0.03 | 1 | 0.03
Résistance 30mR | 0.03 | 3 | 0.09
Résistance 1k | 0.03 | 1 | 0.03
Résistance 32k | 0.03 | 1 | 0.03
DHT22 | 1.59 | 1 | 1.59 |  | https://fr.aliexpress.com/item/1005004095263998.html?_t=pvid%3A9c2b7dc5-9b42-4f98-ae02-fc9ca62ed9d3
AOP LM358 | 0.236 | 1 | 0.236 |  | https://fr.aliexpress.com/item/1005003507912340.html?curPageLogUid=ZY2jVpYmhSdq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
Circuit imprimé | 9.33 | 1 | 9.33
 |  | Total | 25.817
Module maître | PU | Qté | Tot TTC |  | Lien ALI
ESP | 12
Module RS485

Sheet: CMS
Module esclave
Description | PU | Qté | Tot TTC | Lien ALI
Nano 168P | 2.91 | 1 | 2.91
Module RS485 | 0.7 | 1 | 0.7
Alim 12V - 3,3V | 0.81 | 1 | 0.81 | https://fr.aliexpress.com/item/32835853612.html?curPageLogUid=CfbSgzYXkdFU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
Bornier 4 contacts à vis | 1.61 | 2 | 3.22
Bornier 2 contacts à vis | 1.06 | 2 | 2.12
 |  | Total | 9.76
Module maître | PU | Qté | Tot TTC | Lien ALI
ESP | 12
Module RS485

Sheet: THT
Module esclave
Description | PU | Qté | Tot TTC | Lien ALI
ATMEGA168 | 4.28 | 1 | 4.28
Switch | 0.104 | 1 | 0.104
Header 6pts | 0.039 | 1 | 0.039
Condensateur 15pF | 0.107 | 2 | 0.214
Quartz 16MHz | 0.387 | 1 | 0.387
Driver RS485 | 1 | 6.04 | 6.04
Transistor TIP41C | 0.722 | 1 | 0.722
Alim 12V - 3,3V | 0.81 | 1 | 0.81 | https://fr.aliexpress.com/item/32835853612.html?curPageLogUid=CfbSgzYXkdFU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
Bornier 4 contacts à vis | 1.61 | 2 | 3.22
Bornier 2 contacts à vis | 1.06 | 2 | 2.12
 |  | Total | 17.936
Module maître | PU | Qté | Tot TTC | Lien ALI
ESP | 12
Module RS485

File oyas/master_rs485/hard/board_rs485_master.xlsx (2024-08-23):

Source: | C:\DEV\GITHUB\modules_uino\jarduino2\jard_rs485_master\board_rs485_master\board_rs485_master.kicad_sch
Date: | 2024-03-31 18:54
Tool: | Eeschema 7.0.5
Generator: | C:\Program Files\KiCad\7.0\bin\scripting\plugins/bom_csv_grouped_by_value.py
Component Count: | 56
Collated Components:
Item | Qty | Reference(s) | Value | Footprint
1 | 4 | C1, C8, C13, C15 | 10ÂµF | Capacitor_THT:CP_Radial_D4.0mm_P2.00mm
2 | 7 | C2, C5, C6, C7, C11, C12, C14 | 100nF | Capacitor_THT:C_Disc_D5.0mm_W2.5mm_P2.50mm
3 | 3 | C3, C9, C10 | 1nF | Capacitor_THT:C_Disc_D5.0mm_W2.5mm_P2.50mm
4 | 1 | C4 | 100ÂµF | Capacitor_THT:CP_Radial_D8.0mm_P3.80mm
5 | 2 | D1, D2 | D | Diode_THT:D_A-405_P2.54mm_Vertical_AnodeUp
6 | 1 | D3 | D | Diode_THT:D_A-405_P12.70mm_Horizontal
7 | 1 | D4 | SM712_SOT23 | Package_TO_SOT_SMD:SOT-23
8 | 2 | D5, D6 | SD12_SOD323 | Diode_SMD:D_SOD-323
9 | 2 | F1, F2 | Fuse | Fuse:Fuseholder_TR5_Littelfuse_No560_No460
10 | 1 | J1 | POWER_12V | TerminalBlock_Phoenix:TerminalBlock_Phoenix_MKDS-1,5-2-5.08_1x02_P5.08mm_Horizontal
11 | 1 | J2 | Log | Connector_JST:JST_XH_B4B-XH-AM_1x04_P2.50mm_Vertical
12 | 1 | J3 | POWER_OYAS_12V | TerminalBlock_Phoenix:TerminalBlock_Phoenix_MKDS-1,5-2-5.08_1x02_P5.08mm_Horizontal
13 | 1 | J4 | BUS_OYAS | TerminalBlock_Phoenix:TerminalBlock_Phoenix_MKDS-1,5-4-5.08_1x04_P5.08mm_Horizontal
14 | 1 | J5 | Leds RGB | Connector_JST:JST_XH_B3B-XH-AM_1x03_P2.50mm_Vertical
15 | 1 | J6 | Button | Connector_PinHeader_2.54mm:PinHeader_1x02_P2.54mm_Vertical
16 | 1 | Q1 | BPC_2N2222A | Package_TO_SOT_THT:TO-92
17 | 1 | Q2 | BPC_IPP034N03L | Package_TO_SOT_THT:TO-220-3_Vertical
18 | 2 | Q3, Q4 | BC327 | Package_TO_SOT_THT:TO-92_Inline
19 | 2 | R1, R2 | 10k | Resistor_THT:R_Axial_DIN0204_L3.6mm_D1.6mm_P7.62mm_Horizontal
20 | 5 | R3, R12, R16, R17, R18 | 100 | Resistor_THT:R_Axial_DIN0204_L3.6mm_D1.6mm_P7.62mm_Horizontal
21 | 4 | R4, R8, R9, R15 | 100k | Resistor_THT:R_Axial_DIN0204_L3.6mm_D1.6mm_P7.62mm_Horizontal
22 | 4 | R5, R6, R7, R14 | 220 | Resistor_THT:R_Axial_DIN0204_L3.6mm_D1.6mm_P7.62mm_Horizontal
23 | 1 | R10 | R | Resistor_THT:R_Axial_DIN0204_L3.6mm_D1.6mm_P7.62mm_Horizontal
24 | 1 | R13 | 128 | Resistor_THT:R_Axial_DIN0204_L3.6mm_D1.6mm_P7.62mm_Horizontal
25 | 1 | U1 | RtcArduino | bpc:BPC_RtcArduino
26 | 1 | U2 | BPC_Alim5V | bpc:BPC_Alim5V
27 | 1 | U3 | BPC_ESP8266-01_ESP-01 | bpc:BPC_XCVR_ESP8266-01_ESP-01
28 | 1 | U4 | BPC_Mod485 | bpc:BPC_Mod485
29 | 1 | U5 | LM1117DT-3.3 | Package_TO_SOT_THT:TO-220-3_Vertical

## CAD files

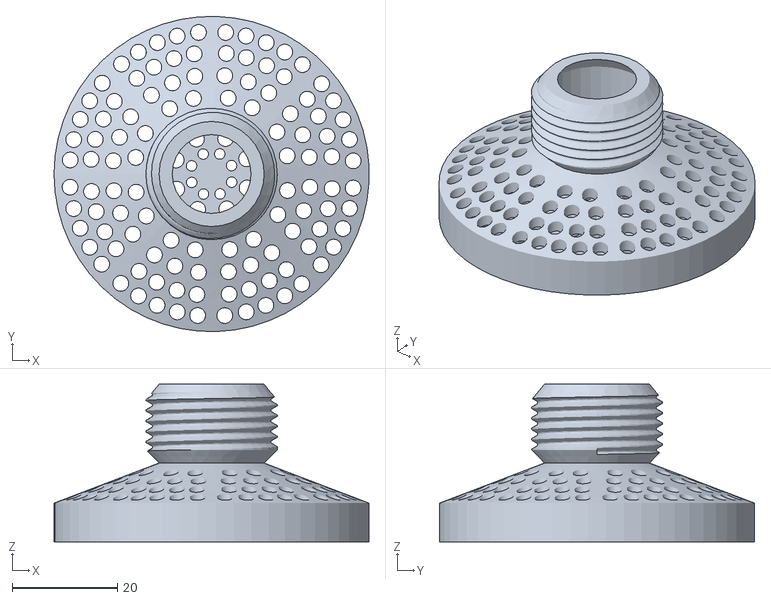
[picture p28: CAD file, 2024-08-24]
cuves/meca/filtreAR-Main.stl
60.0 x 60.0 x 30.0

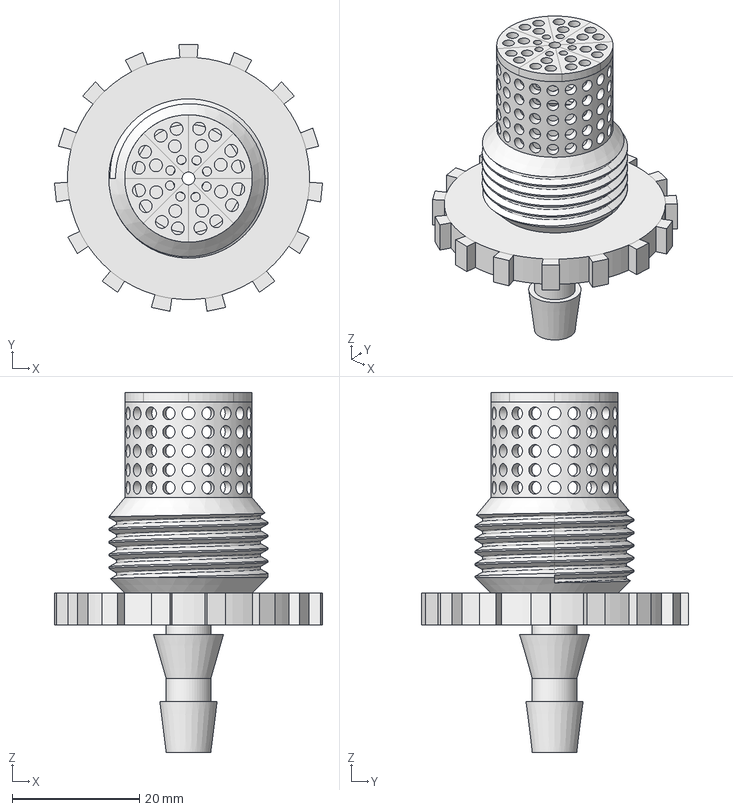
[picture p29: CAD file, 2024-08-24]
cuves/meca/bouchon_filtrant.FCStd
42.1 x 41.9 x 56.5 mm
Grille
Signature en 3D
Annee en 3D
PieceSansGrille

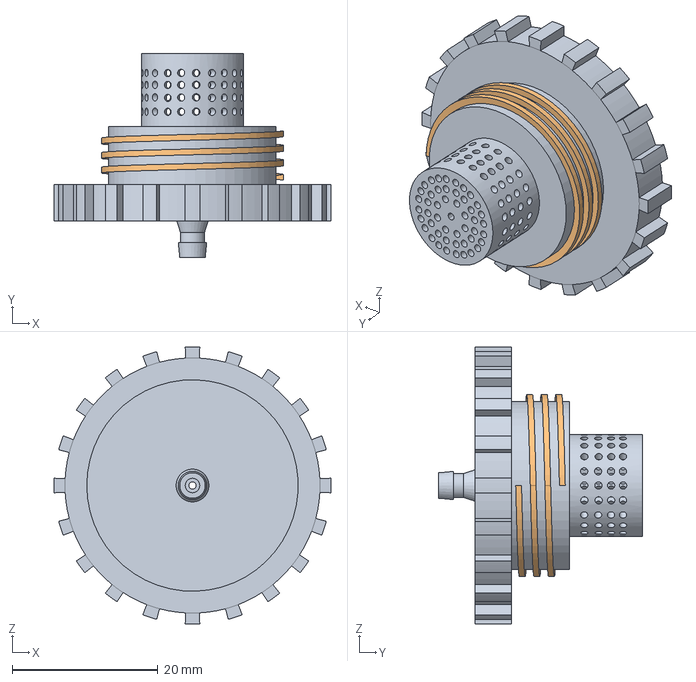
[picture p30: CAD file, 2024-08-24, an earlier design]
cuves/meca/_archives/vis.FCStd
38.0 x 28.0 x 38.0 mm
Profil

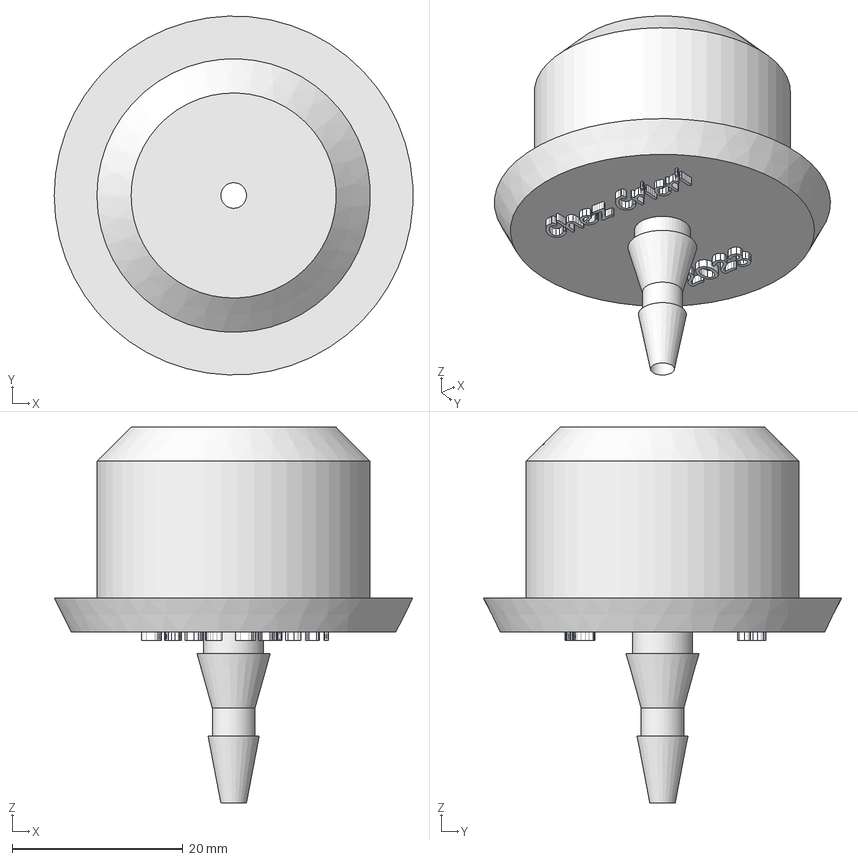
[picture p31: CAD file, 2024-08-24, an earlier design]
cuves/meca/_archives/embout_pressostat.FCStd
42.0 x 42.0 x 44.0 mm
Piece
Annee en 3D
Chez Cricri

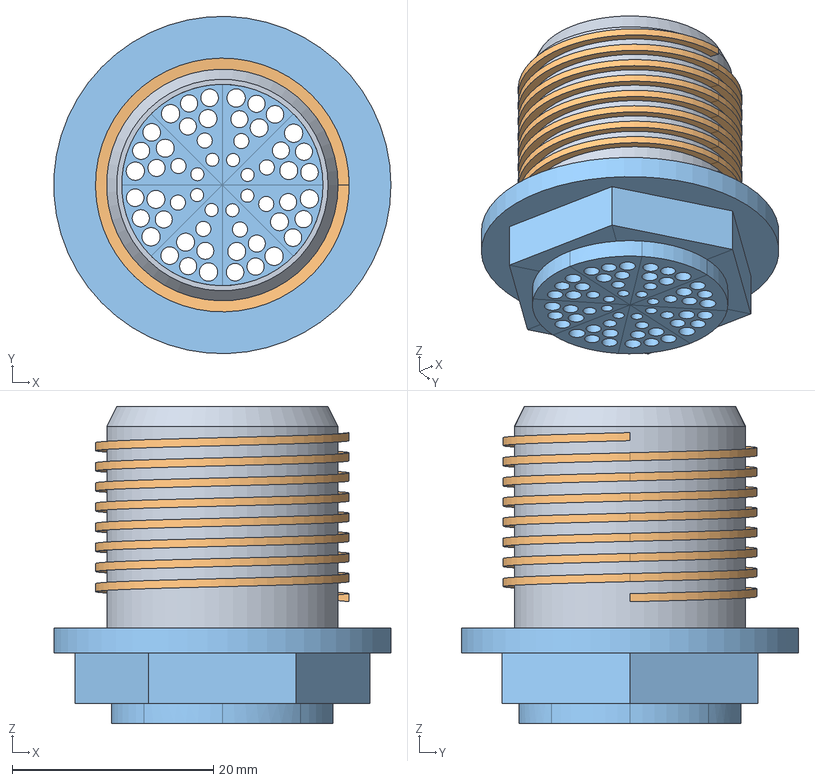
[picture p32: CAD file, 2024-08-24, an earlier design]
cuves/meca/_archives/tube.FCStd
33.5 x 33.5 x 31.5 mm
VisMale
VisMaleFiletage
Tuyau

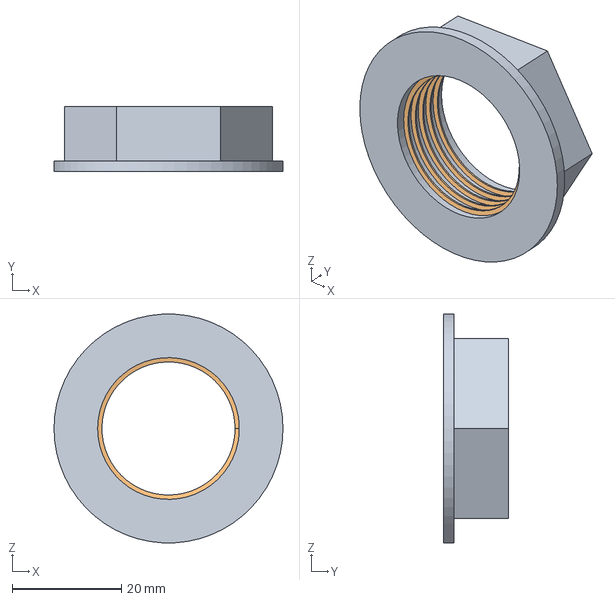
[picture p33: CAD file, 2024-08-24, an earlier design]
cuves/meca/_archives/Ecrou_filetageARevoir.FCStd
42.0 x 12.0 x 41.9 mm

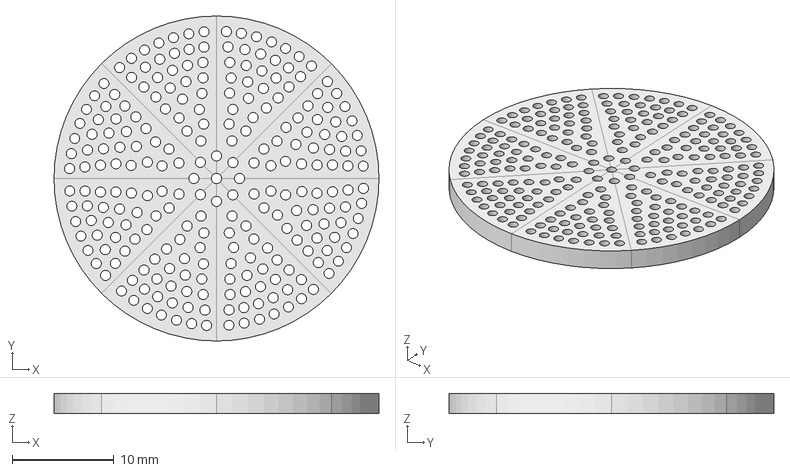
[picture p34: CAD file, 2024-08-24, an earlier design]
cuves/meca/_archives/filtre.FCStd
32.0 x 32.0 x 2.00 mm

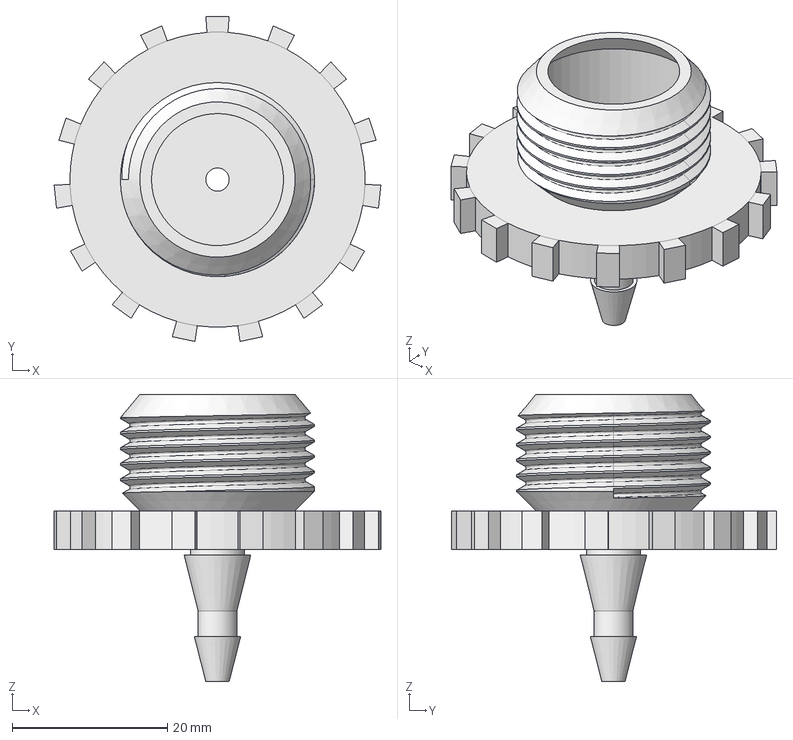
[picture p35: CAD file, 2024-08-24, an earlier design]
cuves/meca/_archives/bouchon_pressostat.FCStd
42.1 x 41.9 x 37.0 mm
Signature en 3D
Annee en 3D
PieceSansGrille

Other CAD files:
cuves/meca/_archives/bouchon_pressostat.stl
cuves/meca/_archives/filtre.stl

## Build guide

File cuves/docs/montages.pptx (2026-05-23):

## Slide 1

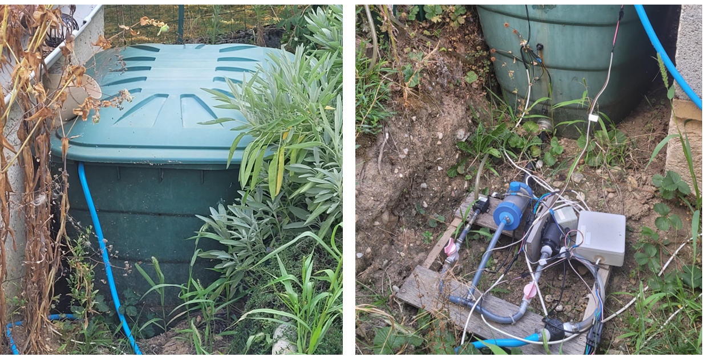
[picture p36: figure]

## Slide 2

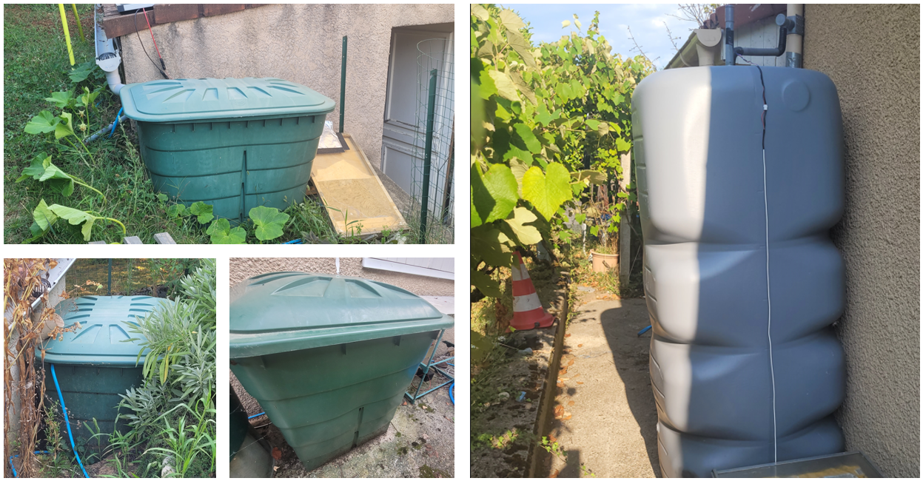
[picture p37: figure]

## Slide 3

Côté réservoir

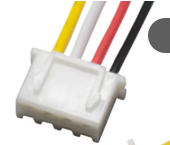
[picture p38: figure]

Milieu (N2)

Bas (N1)

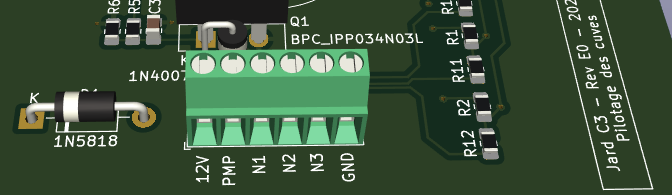
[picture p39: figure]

Haut (N3)

Commun (Gnd)

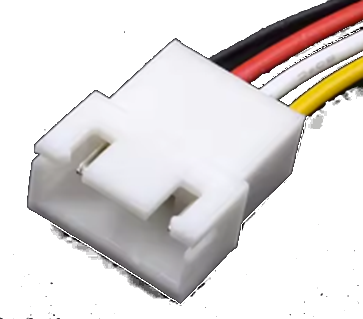
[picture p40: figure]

Côté Carte

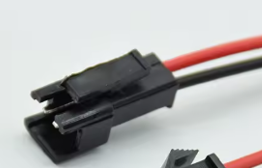
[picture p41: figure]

Alimentation:
- Rouge: 12V
- Noir: Gnd

Commun (Gnd)

Bas (N1)

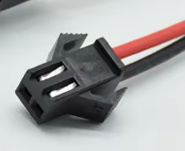
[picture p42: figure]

Milieu (N2)

Haut (N3)

Commande pompe:
- Rouge: 12V
- Noir: PMP

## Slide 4

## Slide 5

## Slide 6

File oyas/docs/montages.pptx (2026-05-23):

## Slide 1

@6

@5

@4

@3

@2

Cuve
100L

Oya

Oya

Oya

Oya

Oya

Pompe

520L

@1

Oya

Oya

Maître
Barbec

@7

@8

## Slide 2

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
Pompe

520L

@1

Oya

@6

Maître
Réduit

Oya

@5

Oya

@4

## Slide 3

300L

Pompe

Maître
Nord

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
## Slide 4

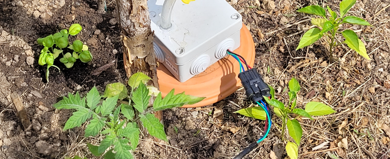
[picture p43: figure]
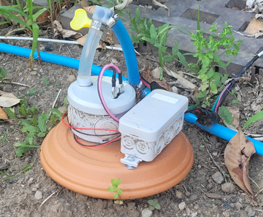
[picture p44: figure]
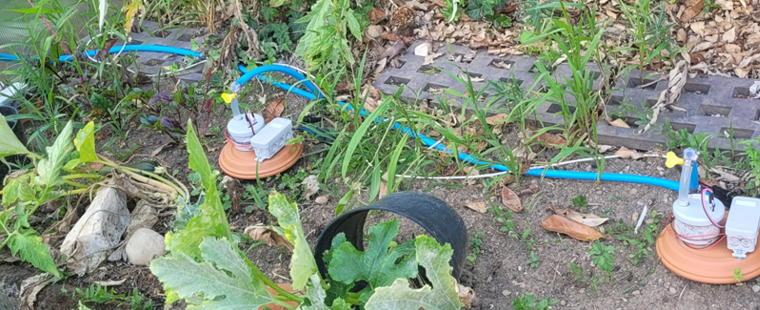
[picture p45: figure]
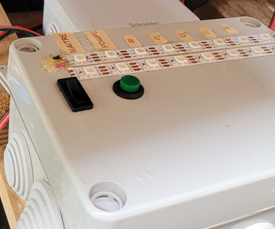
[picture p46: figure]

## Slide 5

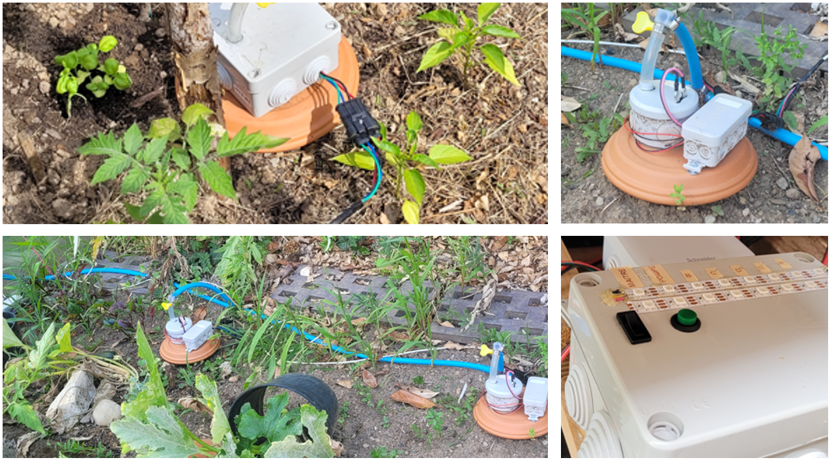
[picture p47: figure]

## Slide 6

SOH

LEN

ID

DATAS

CS

STX

SOH

09

m

CMDS

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
TICK

TEMP

HUM

VOLT

TOT TIME

TOT ERRS

FLOW

CS

STX

SOH

LEN

p

@

ST

TICK

TEMP

HUM

VOLT

TOT TIME

TOT ERRS

CS

STX

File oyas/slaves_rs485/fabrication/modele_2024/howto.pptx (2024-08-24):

## Réalisation d'un Oya 2024

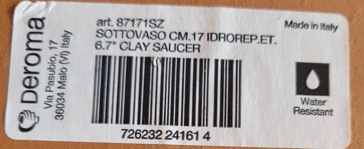
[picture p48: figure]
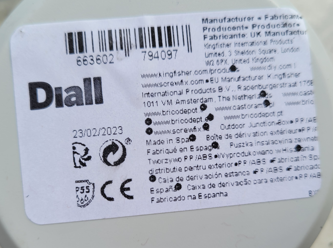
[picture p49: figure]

- Un dessous de vase
- une boîte de dérivation
- un capteur
- une électrovanne

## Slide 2

- Déterminer le centre (avec un compas)
- Tracer un rayon (les 2 trous y seront)
- Percer 12mm à 2,6cm du bord
- Percer 10mm à 6cm du bord

Trou pour tuyau EV: 12 mm
Trou pour jauge: 10 mm

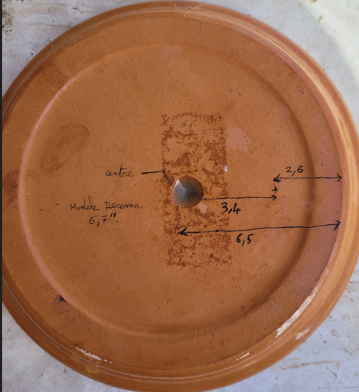
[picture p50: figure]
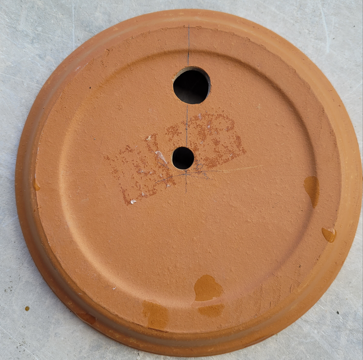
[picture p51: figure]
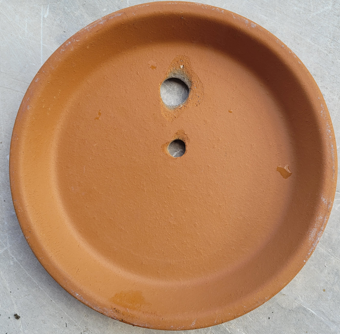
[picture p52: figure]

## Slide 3

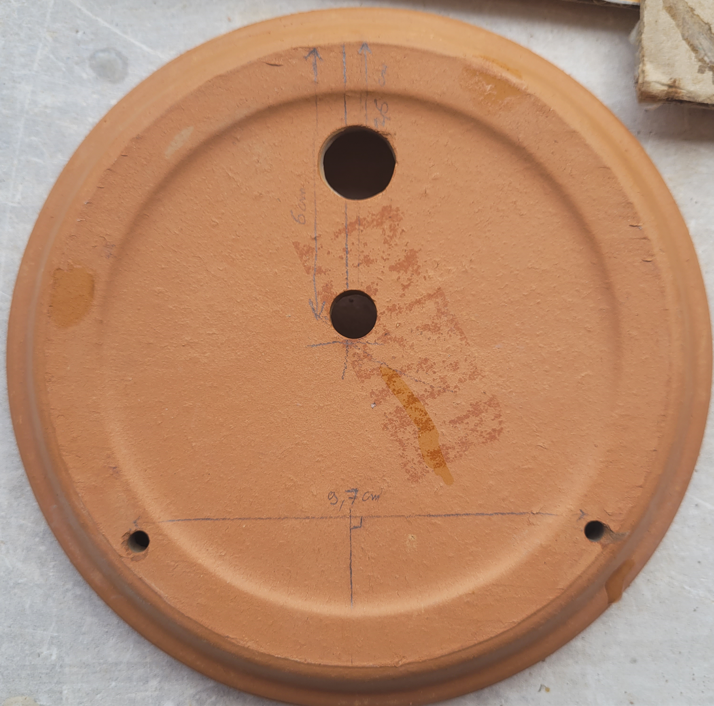
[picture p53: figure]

2 trous 4mm en bas
pour fixer la boîte électronique

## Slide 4

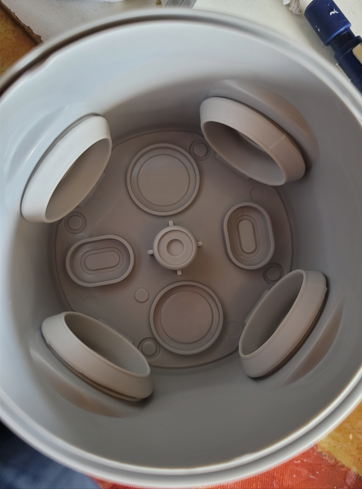
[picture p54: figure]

Perçage 16 mm (tuyau de remplissage vers oya)

Perçage 10 mm (Filetage du capteur de niveau)

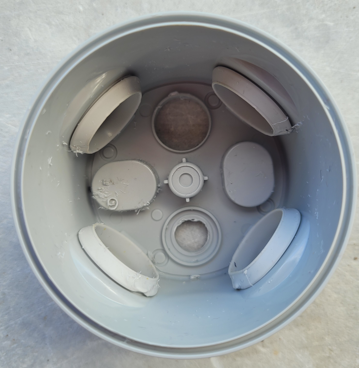
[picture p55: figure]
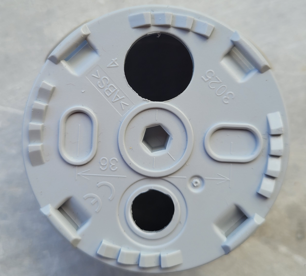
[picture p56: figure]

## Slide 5

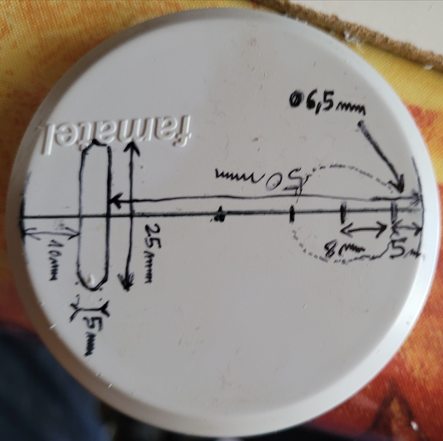
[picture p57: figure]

Diamètre total 6,5 cm (et non 6,5 mm)

- Usiner (à la Dremel) une fente pour les deux cosses
- Percer avec un forêt de 16mm un trou pour l'arrivée d'eau

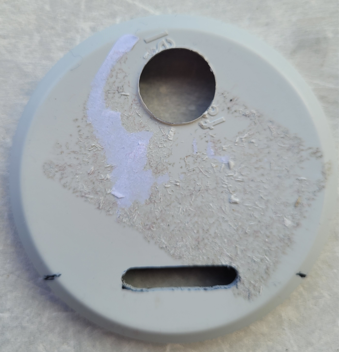
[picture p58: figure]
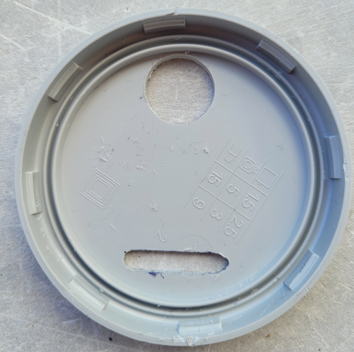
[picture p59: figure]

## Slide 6

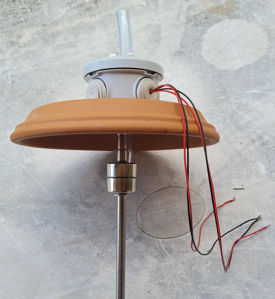
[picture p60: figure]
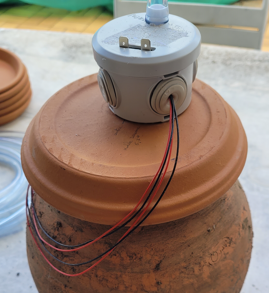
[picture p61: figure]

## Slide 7

Cable Réseau

1 – Rouge : +12V
2 – Noir : Masse
3 – Bleu : Bus A
4 – Vert : Bus B

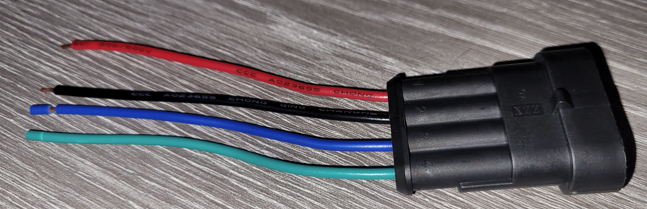
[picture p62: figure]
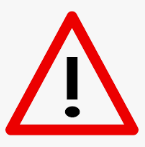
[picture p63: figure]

Certains embouts Ali express
ne respectent pas le code couleur.
Se baser sur le modèle ci-contre.

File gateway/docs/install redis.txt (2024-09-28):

apt-get update
apt-get install redis-server
sudo systemctl enable redis-server
sudo systemctl start redis-server

pip install redis

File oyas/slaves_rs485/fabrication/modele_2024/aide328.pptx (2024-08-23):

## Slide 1

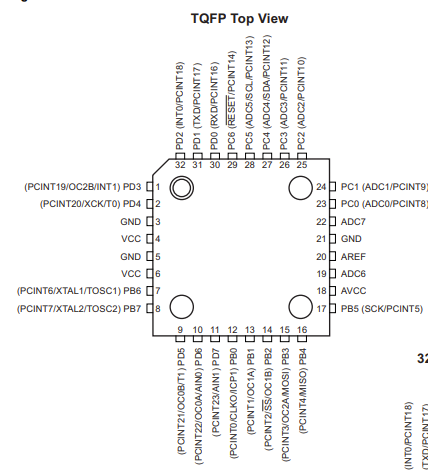
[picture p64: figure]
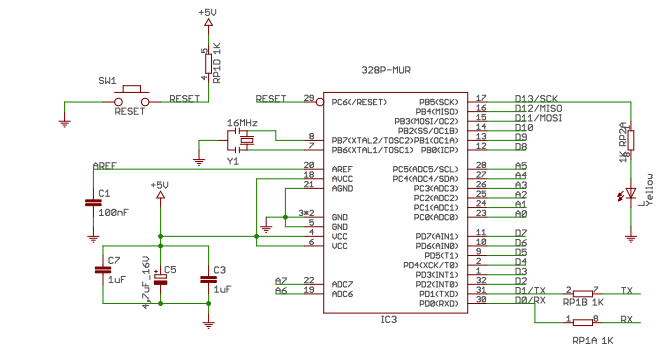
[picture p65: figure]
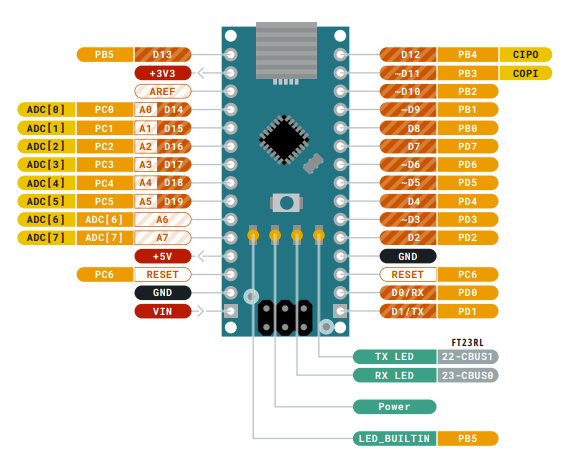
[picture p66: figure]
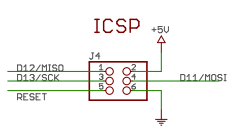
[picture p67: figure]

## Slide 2

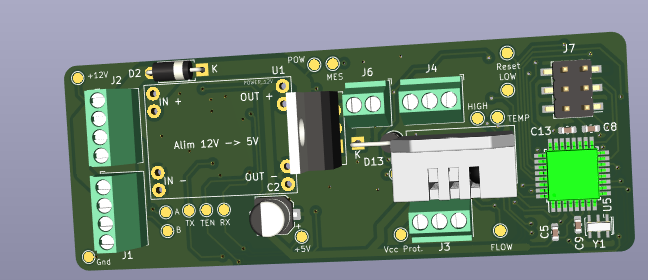
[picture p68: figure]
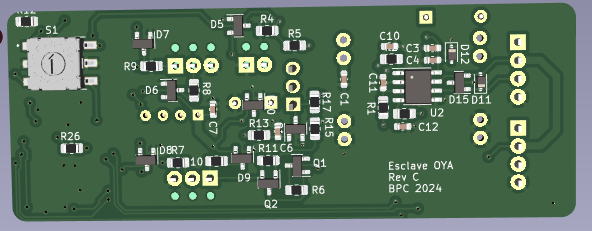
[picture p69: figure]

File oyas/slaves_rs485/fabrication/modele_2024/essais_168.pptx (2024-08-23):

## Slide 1

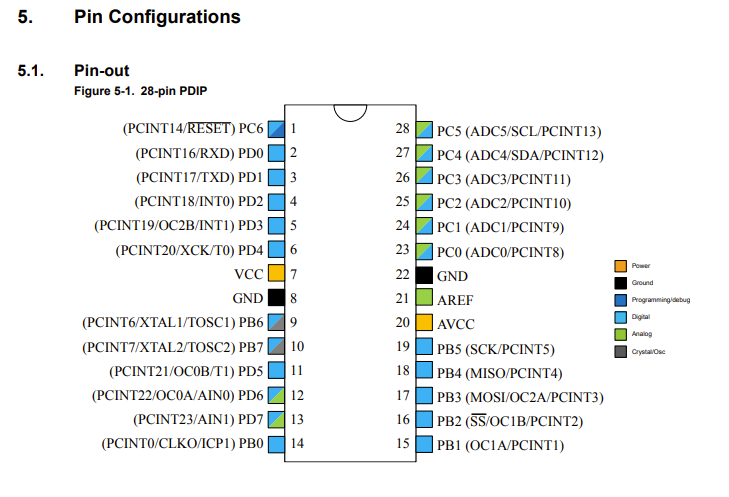
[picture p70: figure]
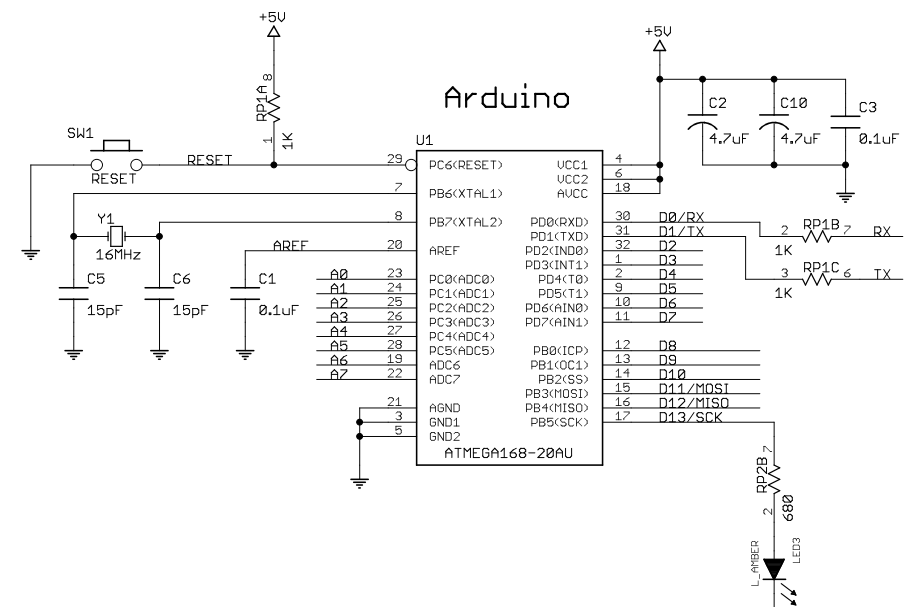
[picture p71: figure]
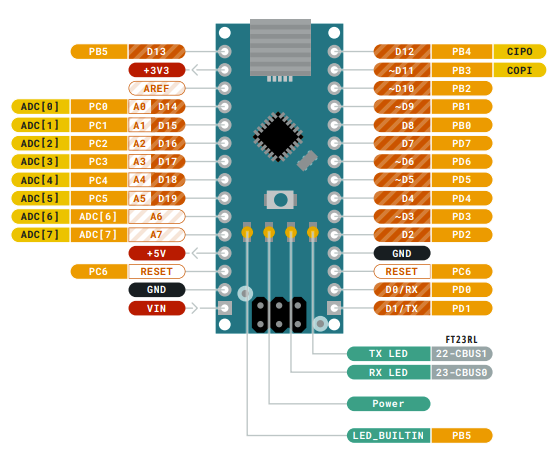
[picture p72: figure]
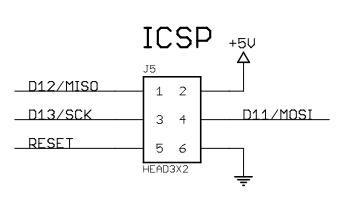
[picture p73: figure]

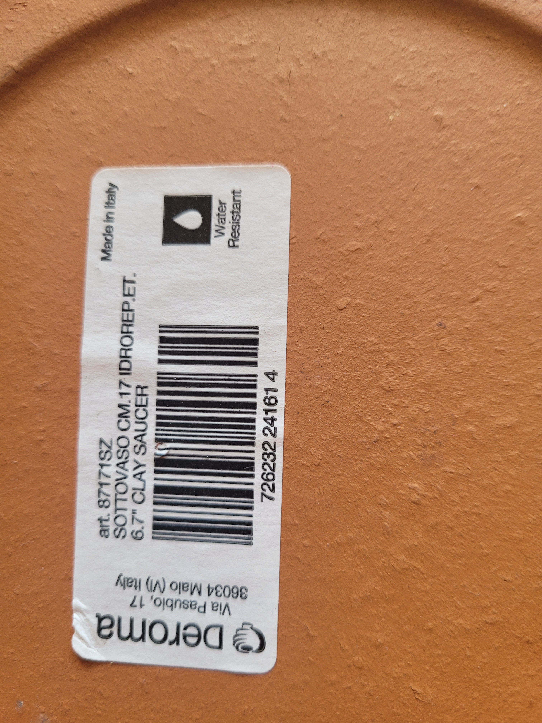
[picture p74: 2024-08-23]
oyas/slaves_rs485/fabrication/modele_2024/photos/20240323_111003.jpg

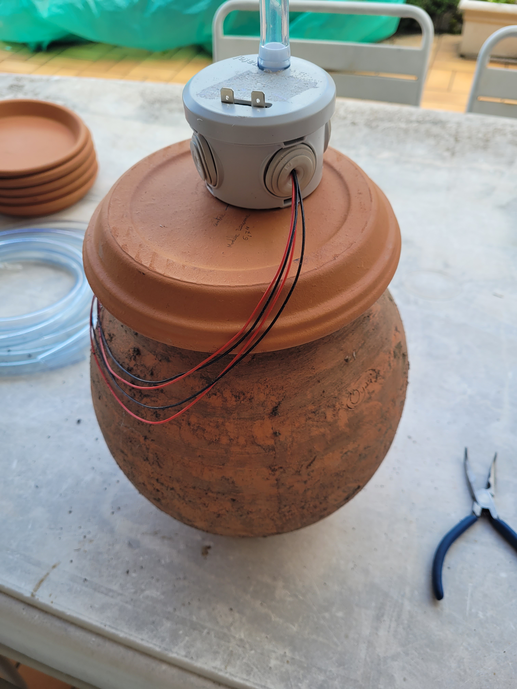
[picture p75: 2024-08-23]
oyas/slaves_rs485/fabrication/modele_2024/photos/20240324_161334.jpg

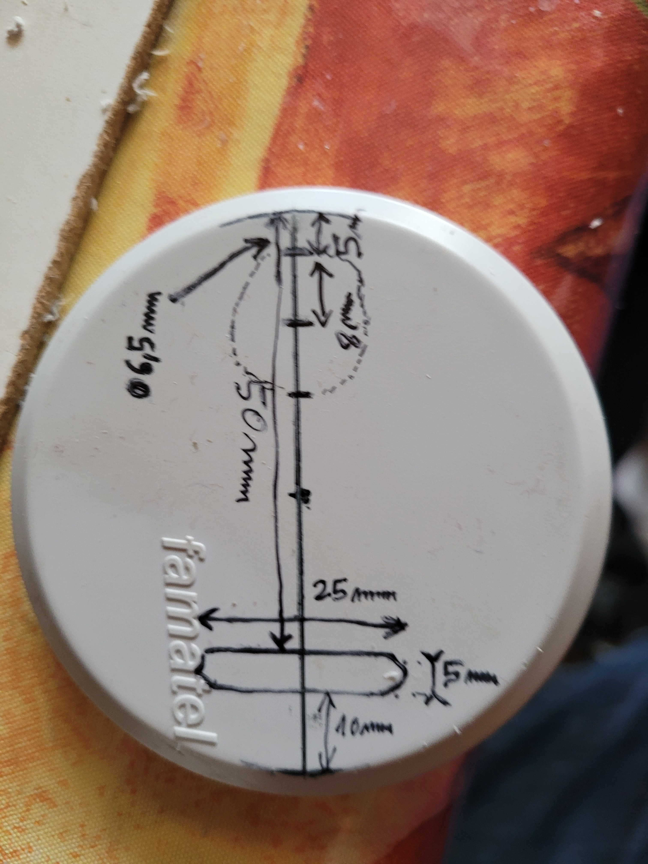
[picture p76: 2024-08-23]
oyas/slaves_rs485/fabrication/modele_2024/photos/20240324_163535.jpg

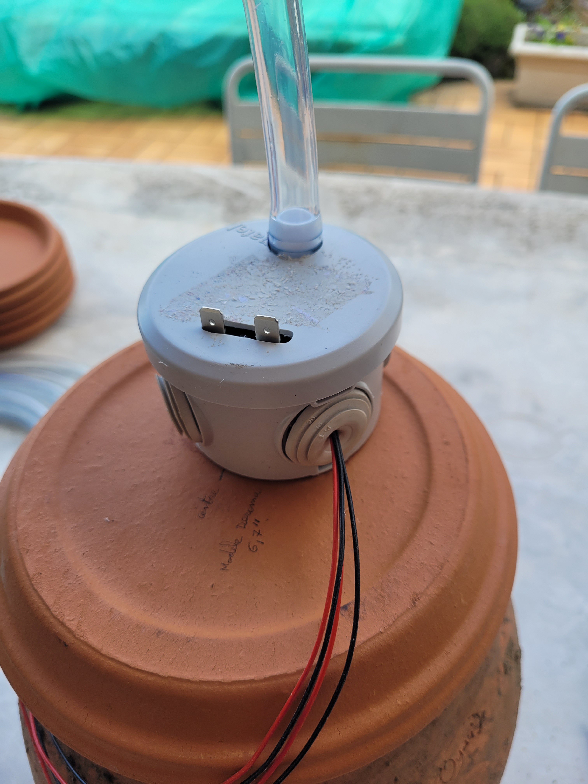
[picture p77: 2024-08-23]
oyas/slaves_rs485/fabrication/modele_2024/photos/20240324_161337.jpg

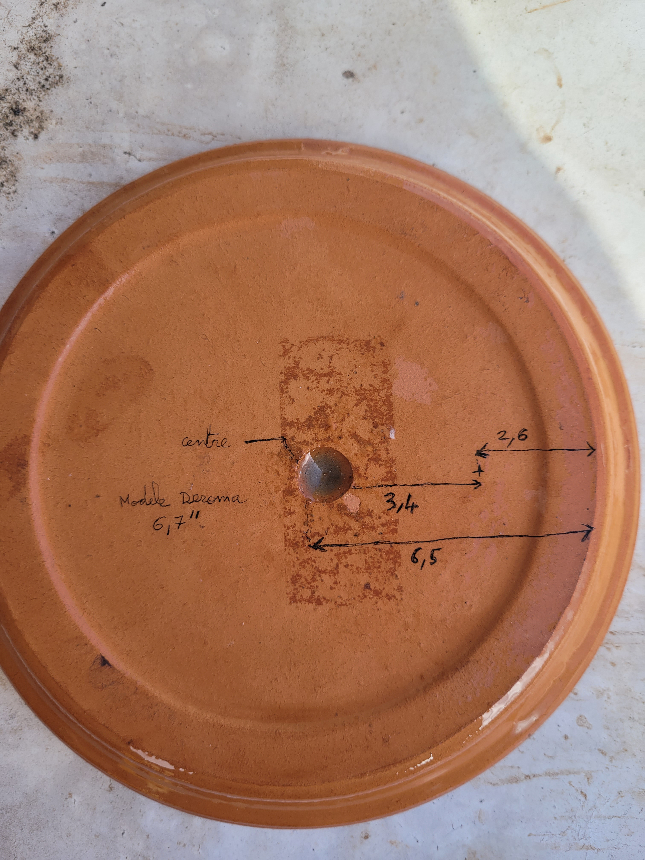
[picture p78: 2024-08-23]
oyas/slaves_rs485/fabrication/modele_2024/photos/20240324_145234.jpg

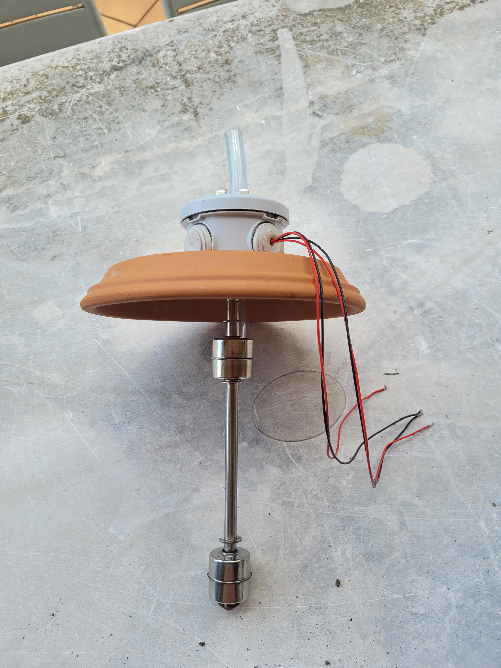
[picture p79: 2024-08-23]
oyas/slaves_rs485/fabrication/modele_2024/photos/20240324_161350.jpg

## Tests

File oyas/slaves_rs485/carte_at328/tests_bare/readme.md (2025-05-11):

# Logiciel de tests "Testsbare"

Ce logiciel permet de mettre en route la carte.

C'est le premier logiciel à utiliser après la câblage des composants.

## Première programmation du micro ATMmega328P

### Programmation des fusibles

A la première programmation du micro, il faut programmer les fusibles de la manière suivante:

Fuse Register | Value
--- | ---
EXTENDED | FD
HIGH | D2
LOW | FF

Cela permet de régler l'horloge sur le quartz externe et de couper le micro si Vcc<2.7V.

Pour programmer les fusibles:
- Aller dans Tools->Device Programming;
- Sélectionner la sonde AVRISP mkII et le device  ATmega328P;
- Faire Apply et lire la signature (Si cela ne marce pas, alors on ne peut pas communiquer avec le micro: Revoir les soudures ?);
- Aller dans Fuses, régler les fusibles puis faire Program

### Chargement du programme de test dans le micro

- Ouvrir le projet
- Aller dans Tools->Device Programming;
- Sélectionner la sonde AVRISP mkII et le device  ATmega328P;
- Faire Apply et lire la signature (Si cela ne marce pas, alors on ne peut pas communiquer avec le micro: Revoir les soudures ?);
- Aller dans Memories
- Dans la partie Flash, faire Program

## Objectif et mode d'emploi

On peut ou non utiliser la puce RS485 avec le #define ENABLE_RS485 (recompiler le projet).

- Sans ENABLE_RS485, la carte fait clignoter la LED toutes les secondes (permet de donc de vérifier l'horloge)
- Avec le #define ENABLE_RS485, la carte envoi un 'A' toutes les secondes sur le RS485.

Donc il faut juste vérifier que la LED clignote et éventuellement la réception du 'A' sur le bus.

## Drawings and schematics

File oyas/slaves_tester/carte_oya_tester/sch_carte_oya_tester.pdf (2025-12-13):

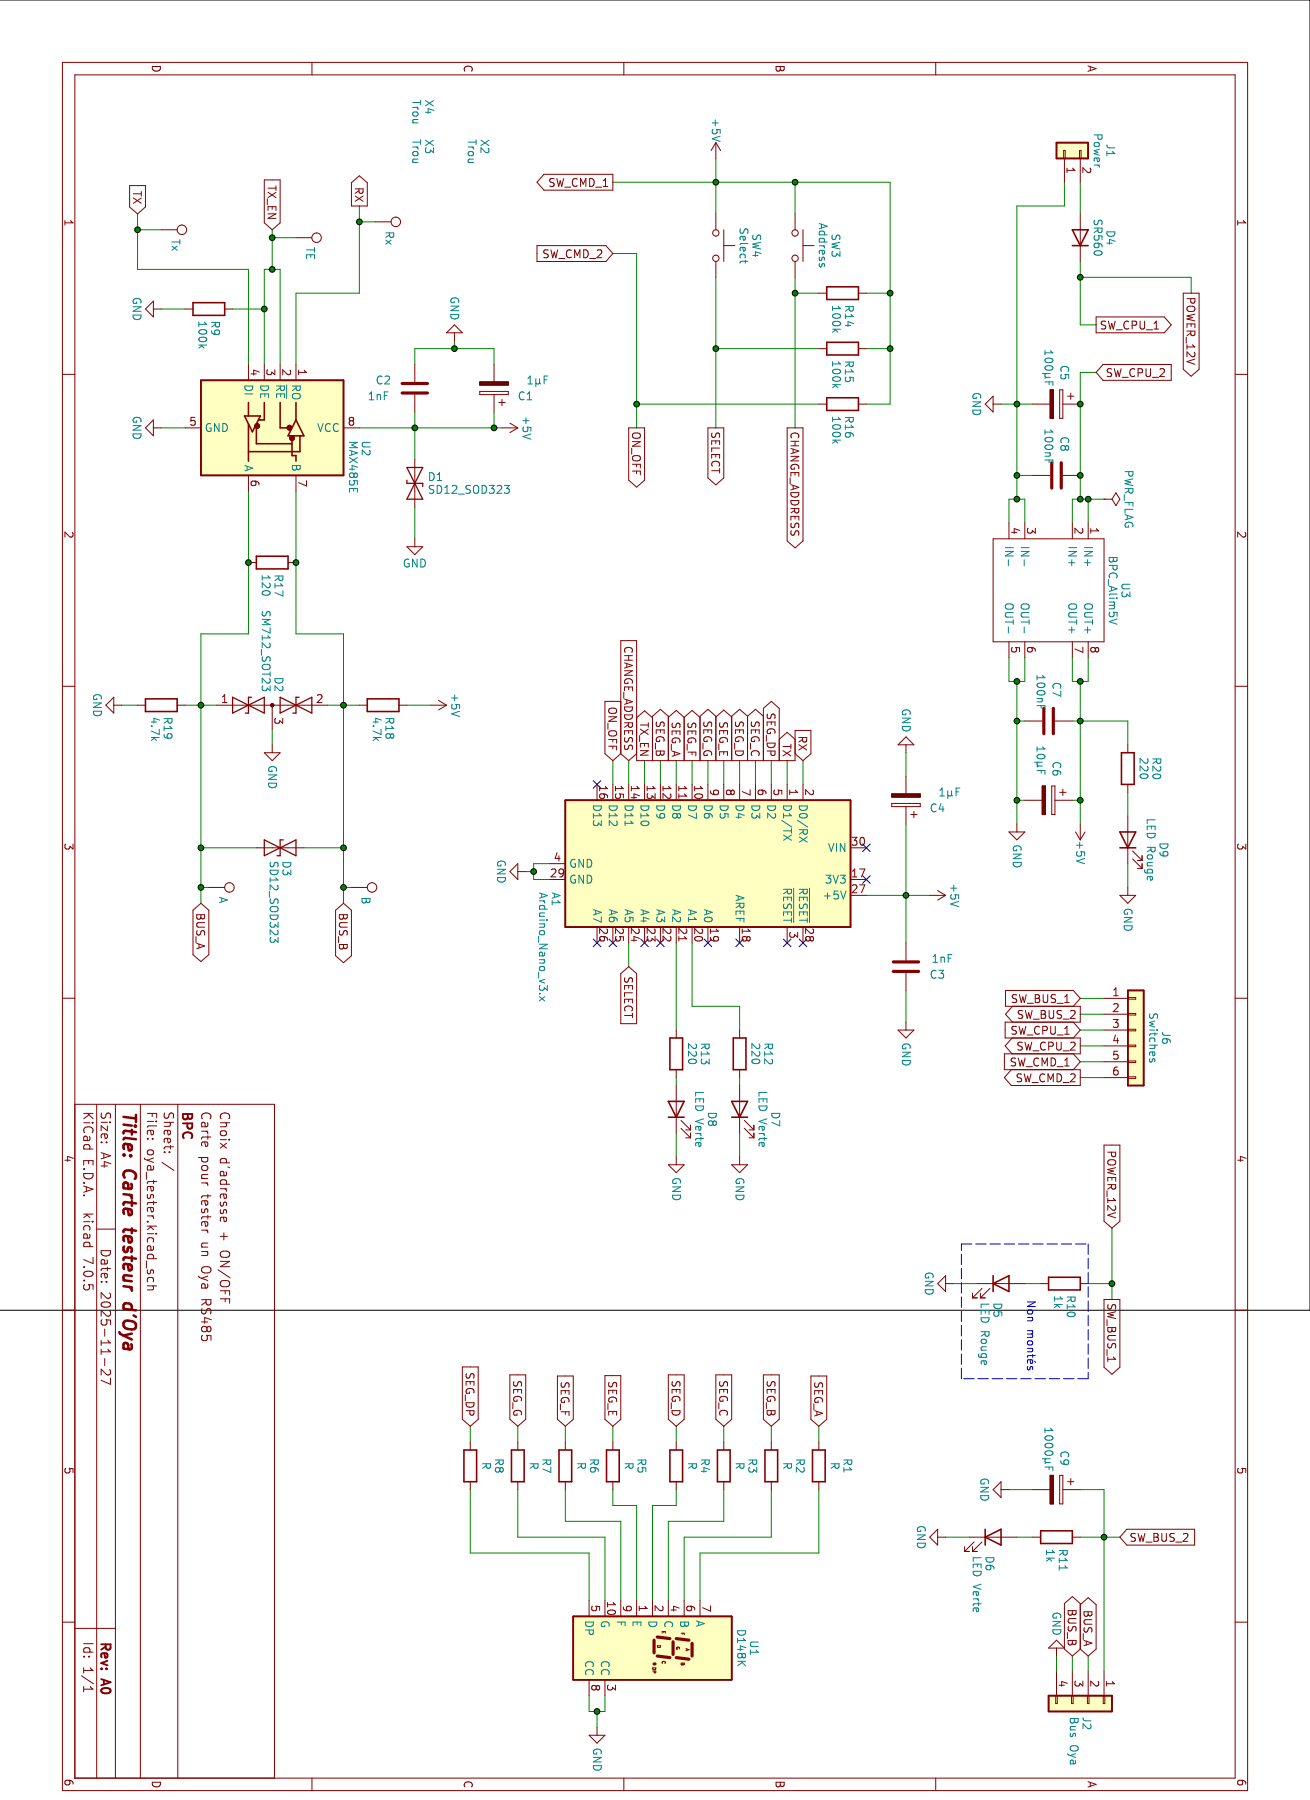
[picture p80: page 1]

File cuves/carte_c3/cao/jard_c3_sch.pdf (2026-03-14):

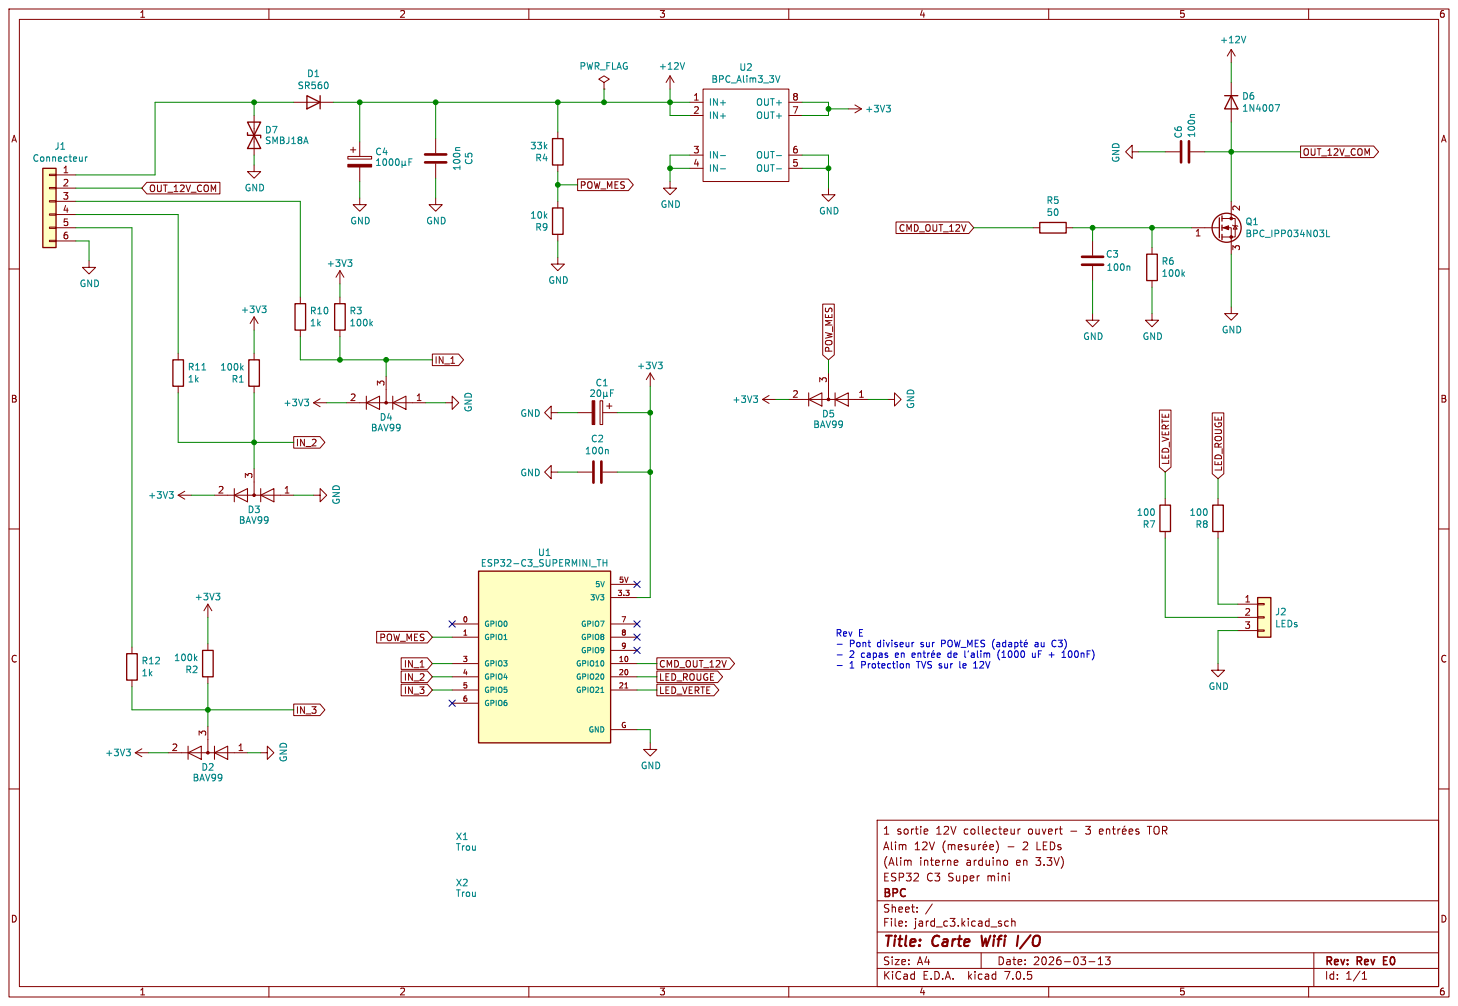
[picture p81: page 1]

- Pont diviseur sur POW_MES þÿ(adapté au C3)

Id: 1/1 Title: Carte Wifi I/O

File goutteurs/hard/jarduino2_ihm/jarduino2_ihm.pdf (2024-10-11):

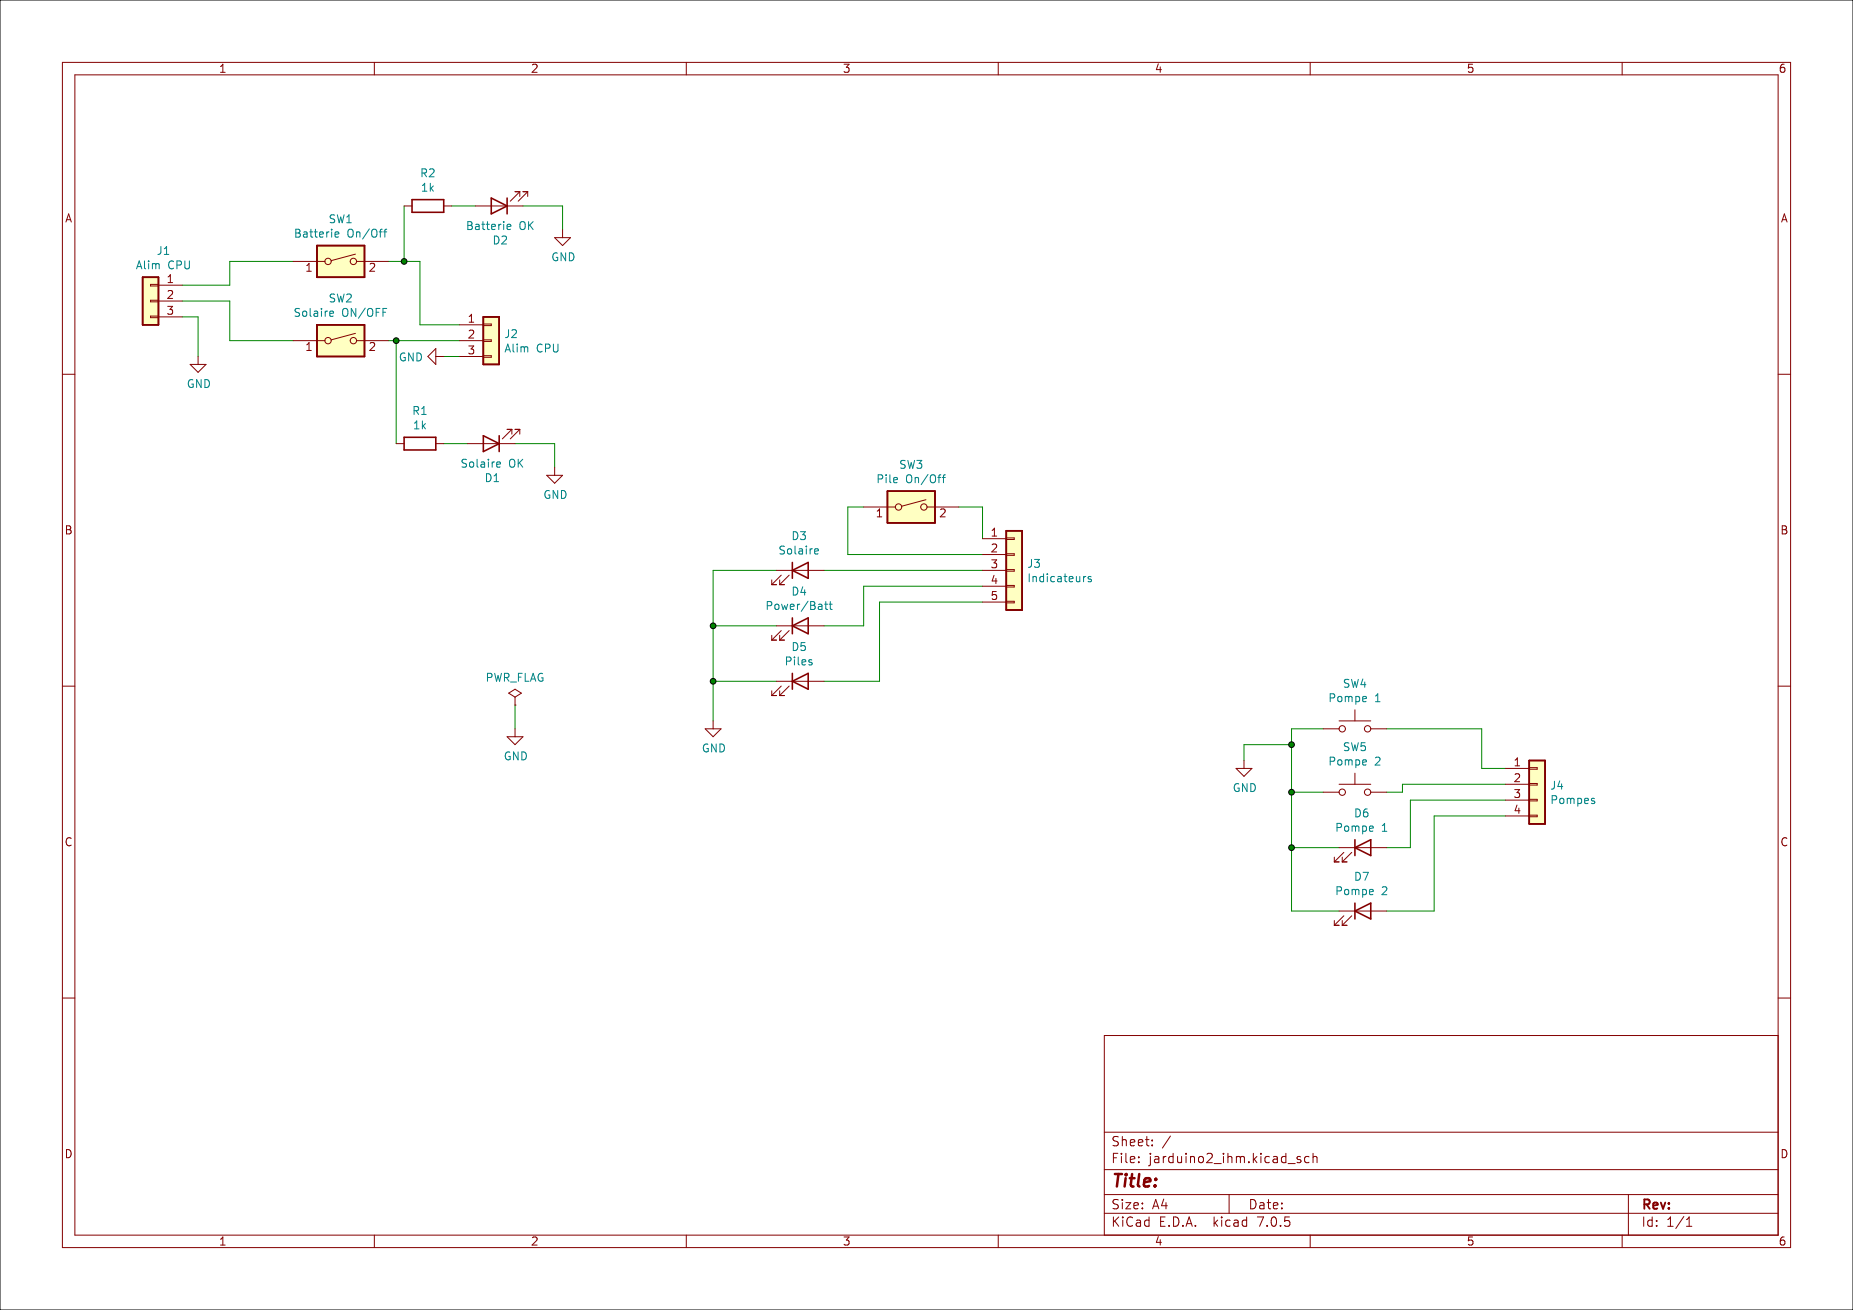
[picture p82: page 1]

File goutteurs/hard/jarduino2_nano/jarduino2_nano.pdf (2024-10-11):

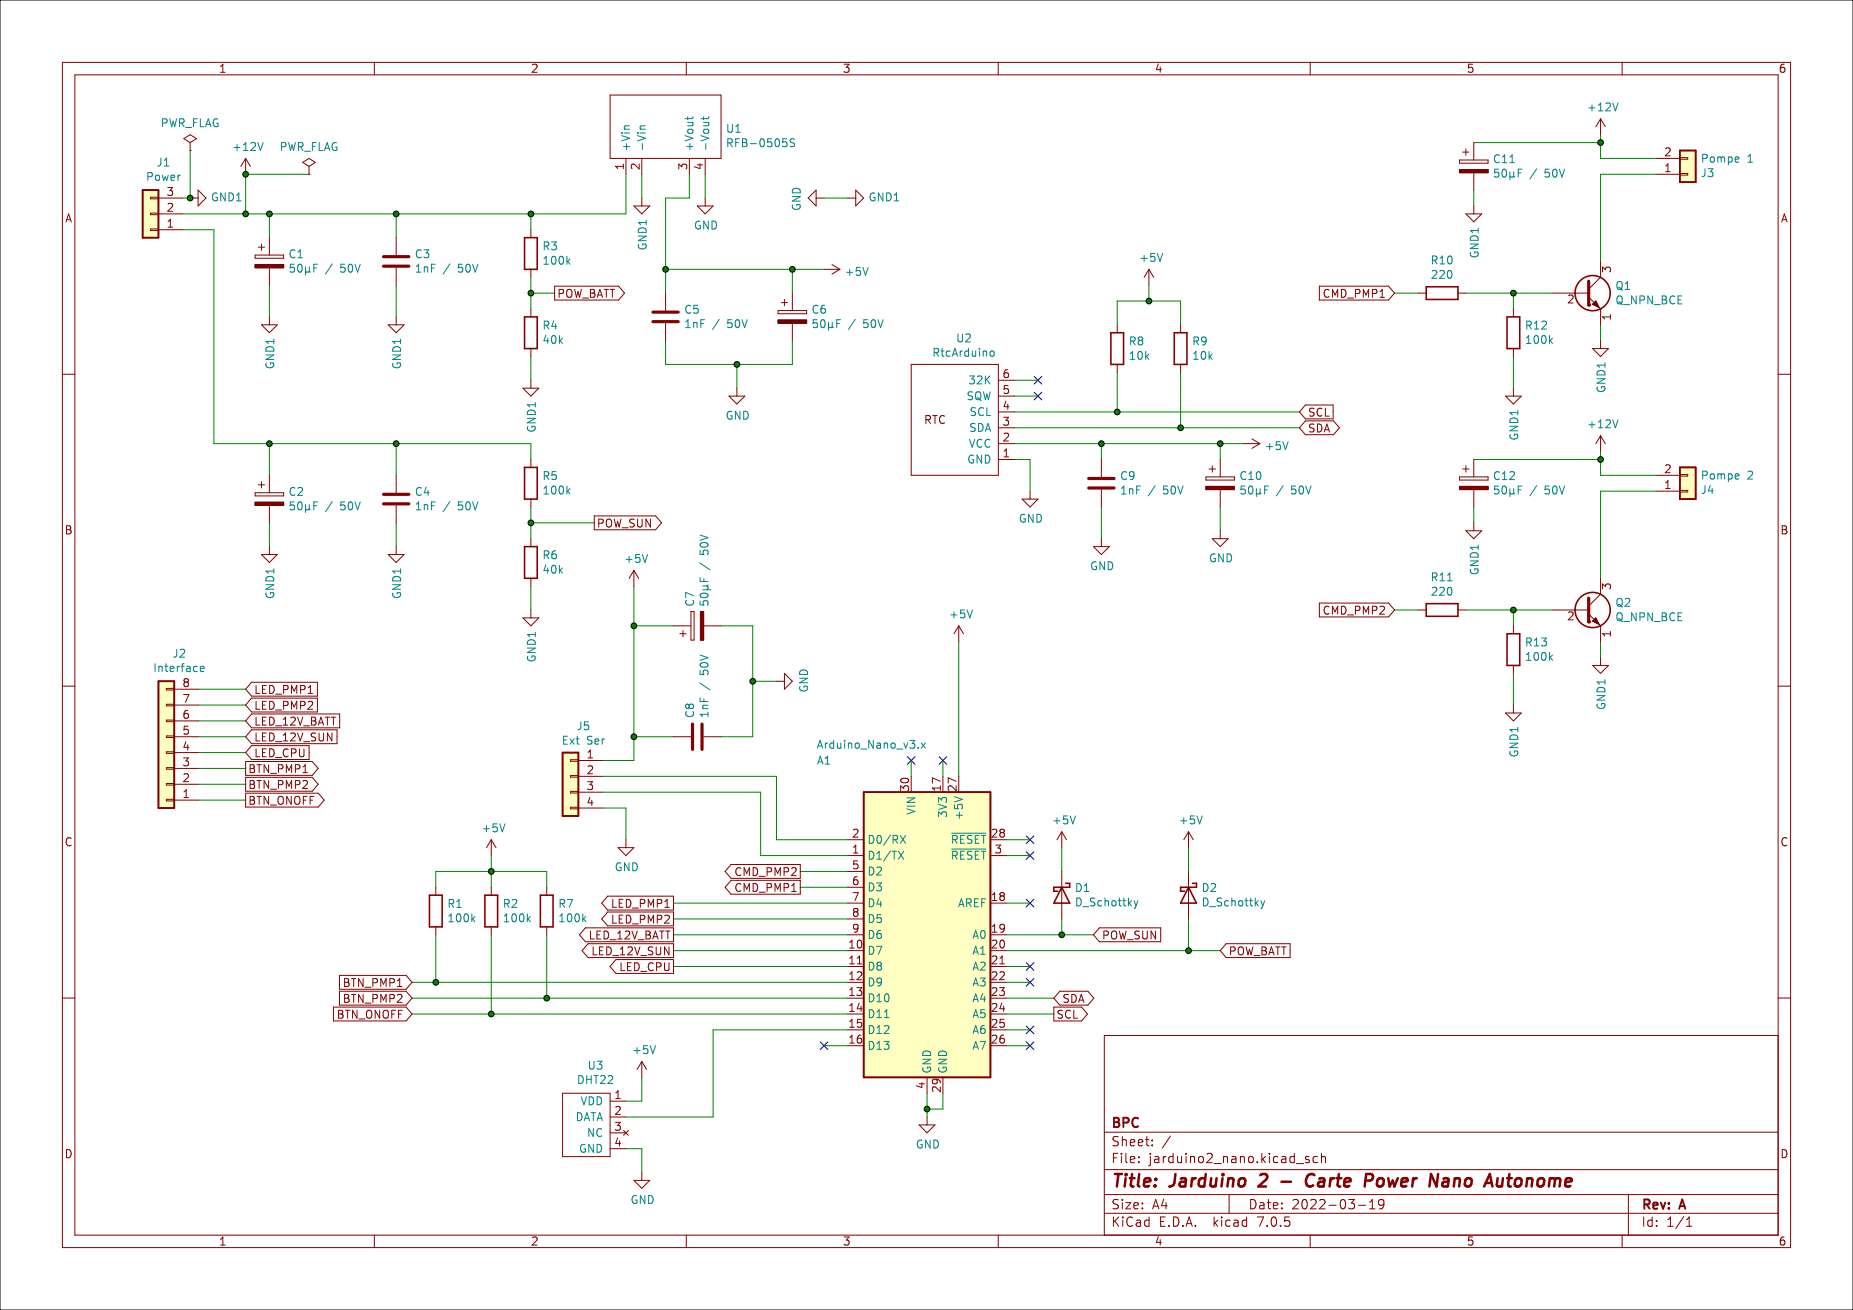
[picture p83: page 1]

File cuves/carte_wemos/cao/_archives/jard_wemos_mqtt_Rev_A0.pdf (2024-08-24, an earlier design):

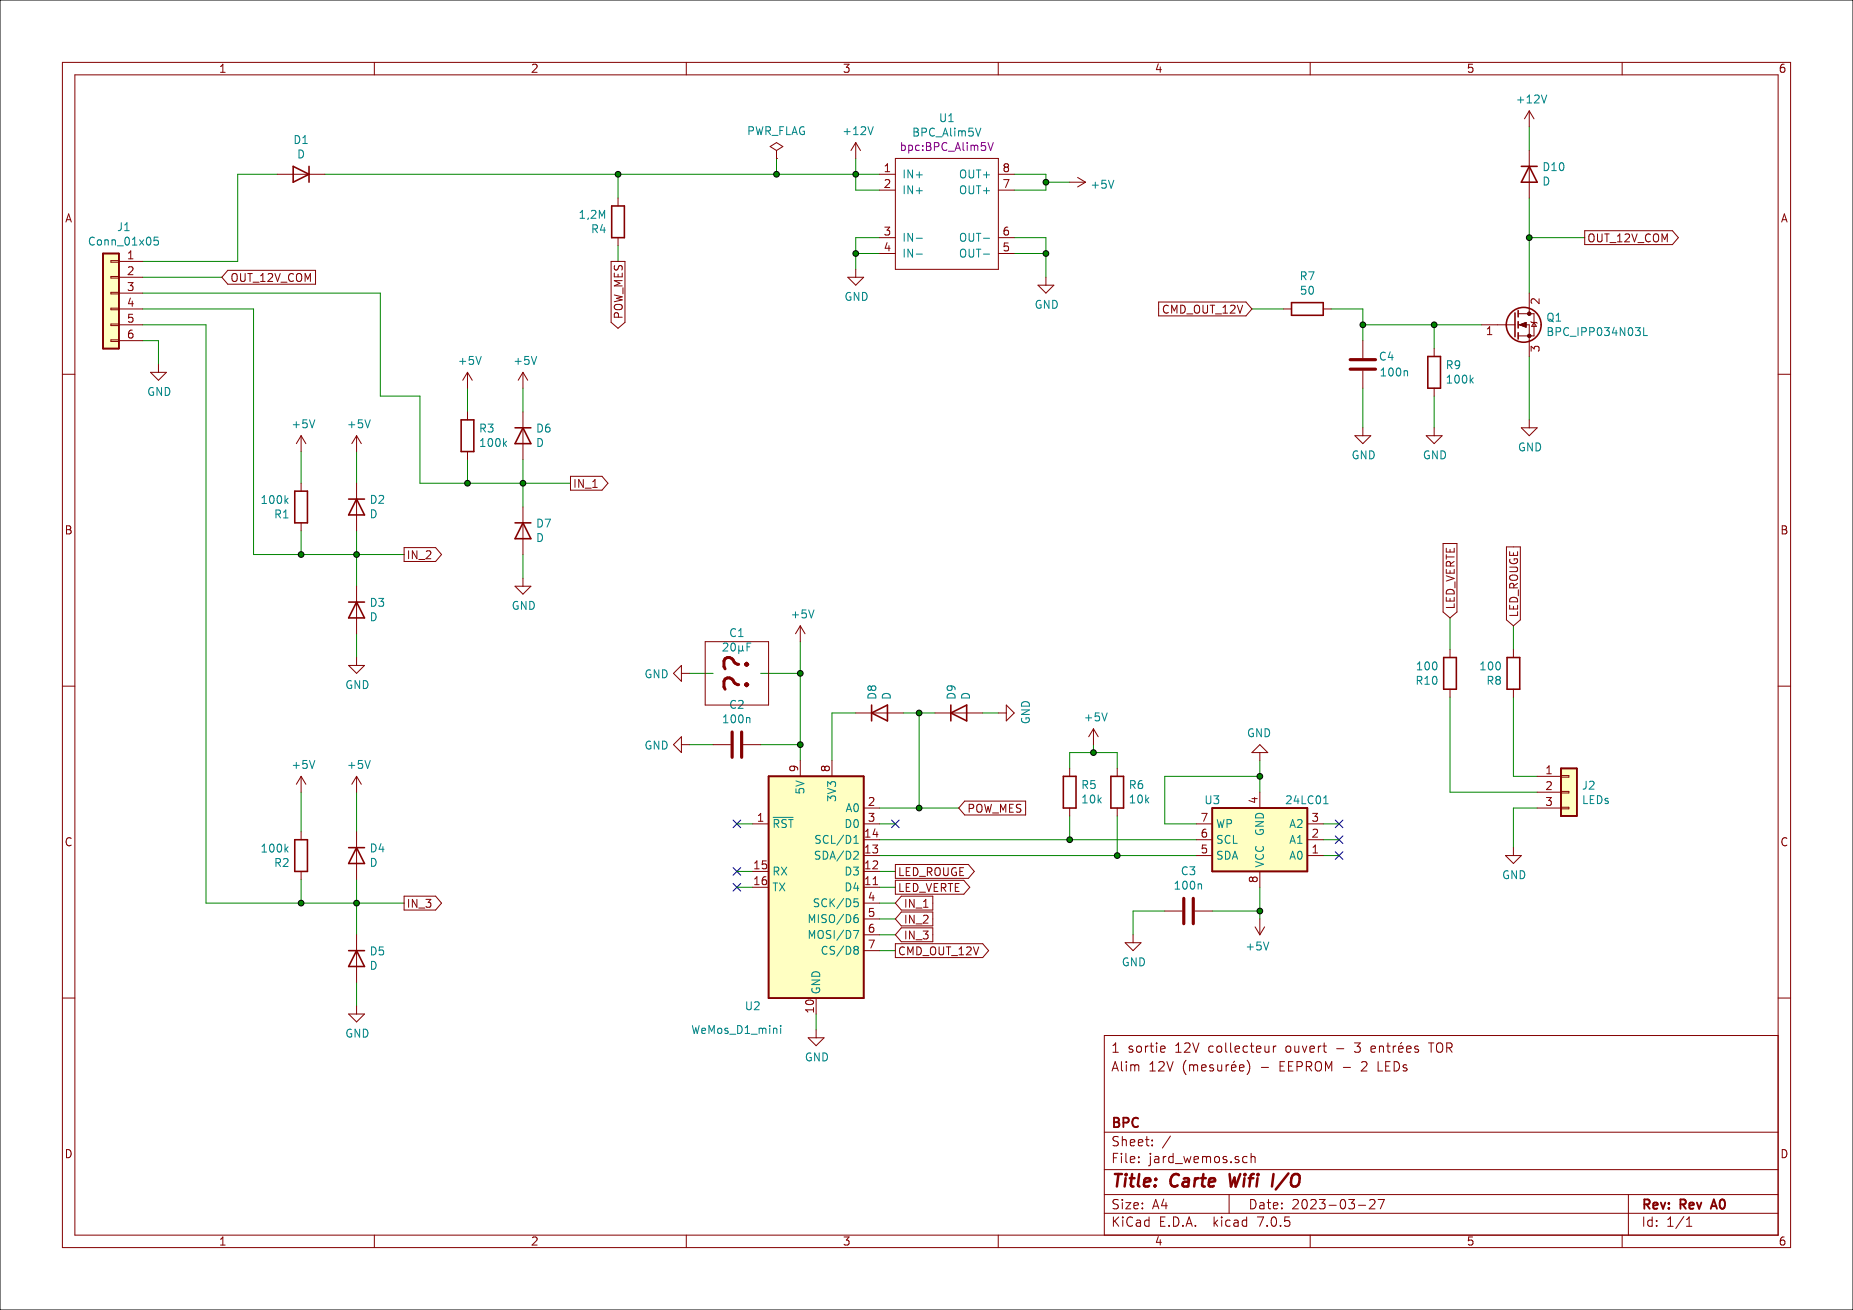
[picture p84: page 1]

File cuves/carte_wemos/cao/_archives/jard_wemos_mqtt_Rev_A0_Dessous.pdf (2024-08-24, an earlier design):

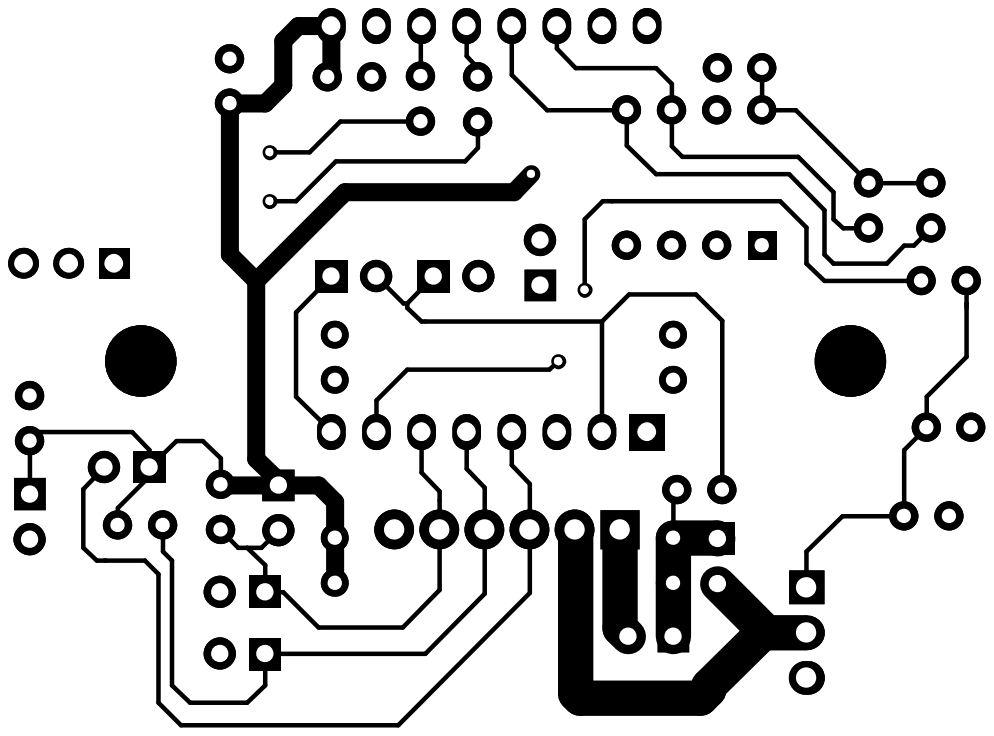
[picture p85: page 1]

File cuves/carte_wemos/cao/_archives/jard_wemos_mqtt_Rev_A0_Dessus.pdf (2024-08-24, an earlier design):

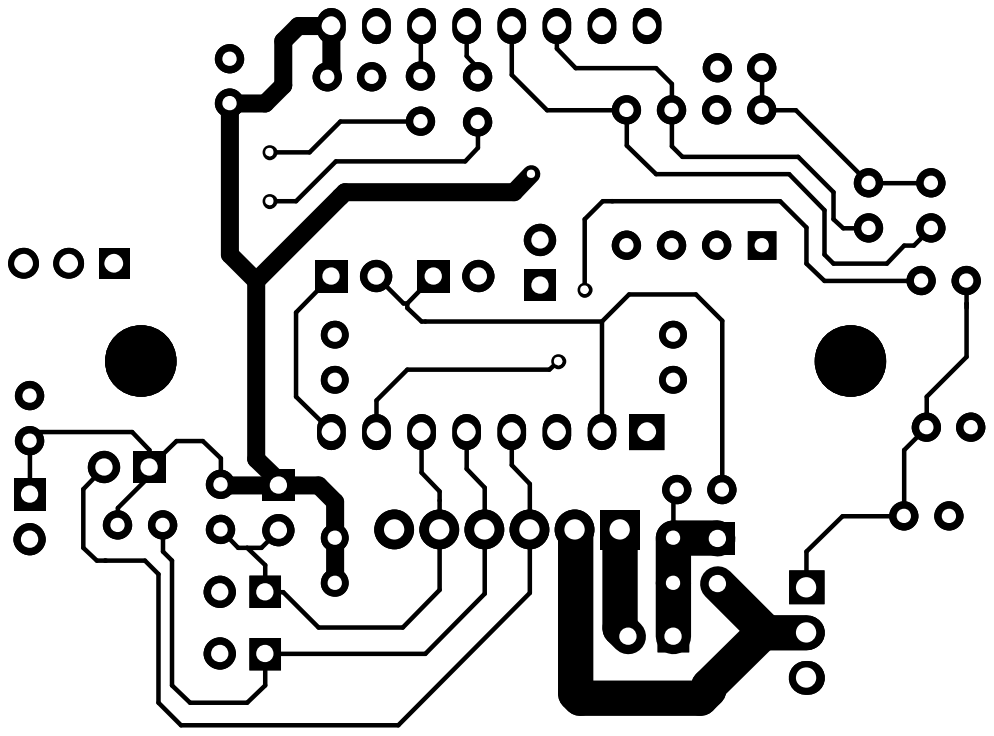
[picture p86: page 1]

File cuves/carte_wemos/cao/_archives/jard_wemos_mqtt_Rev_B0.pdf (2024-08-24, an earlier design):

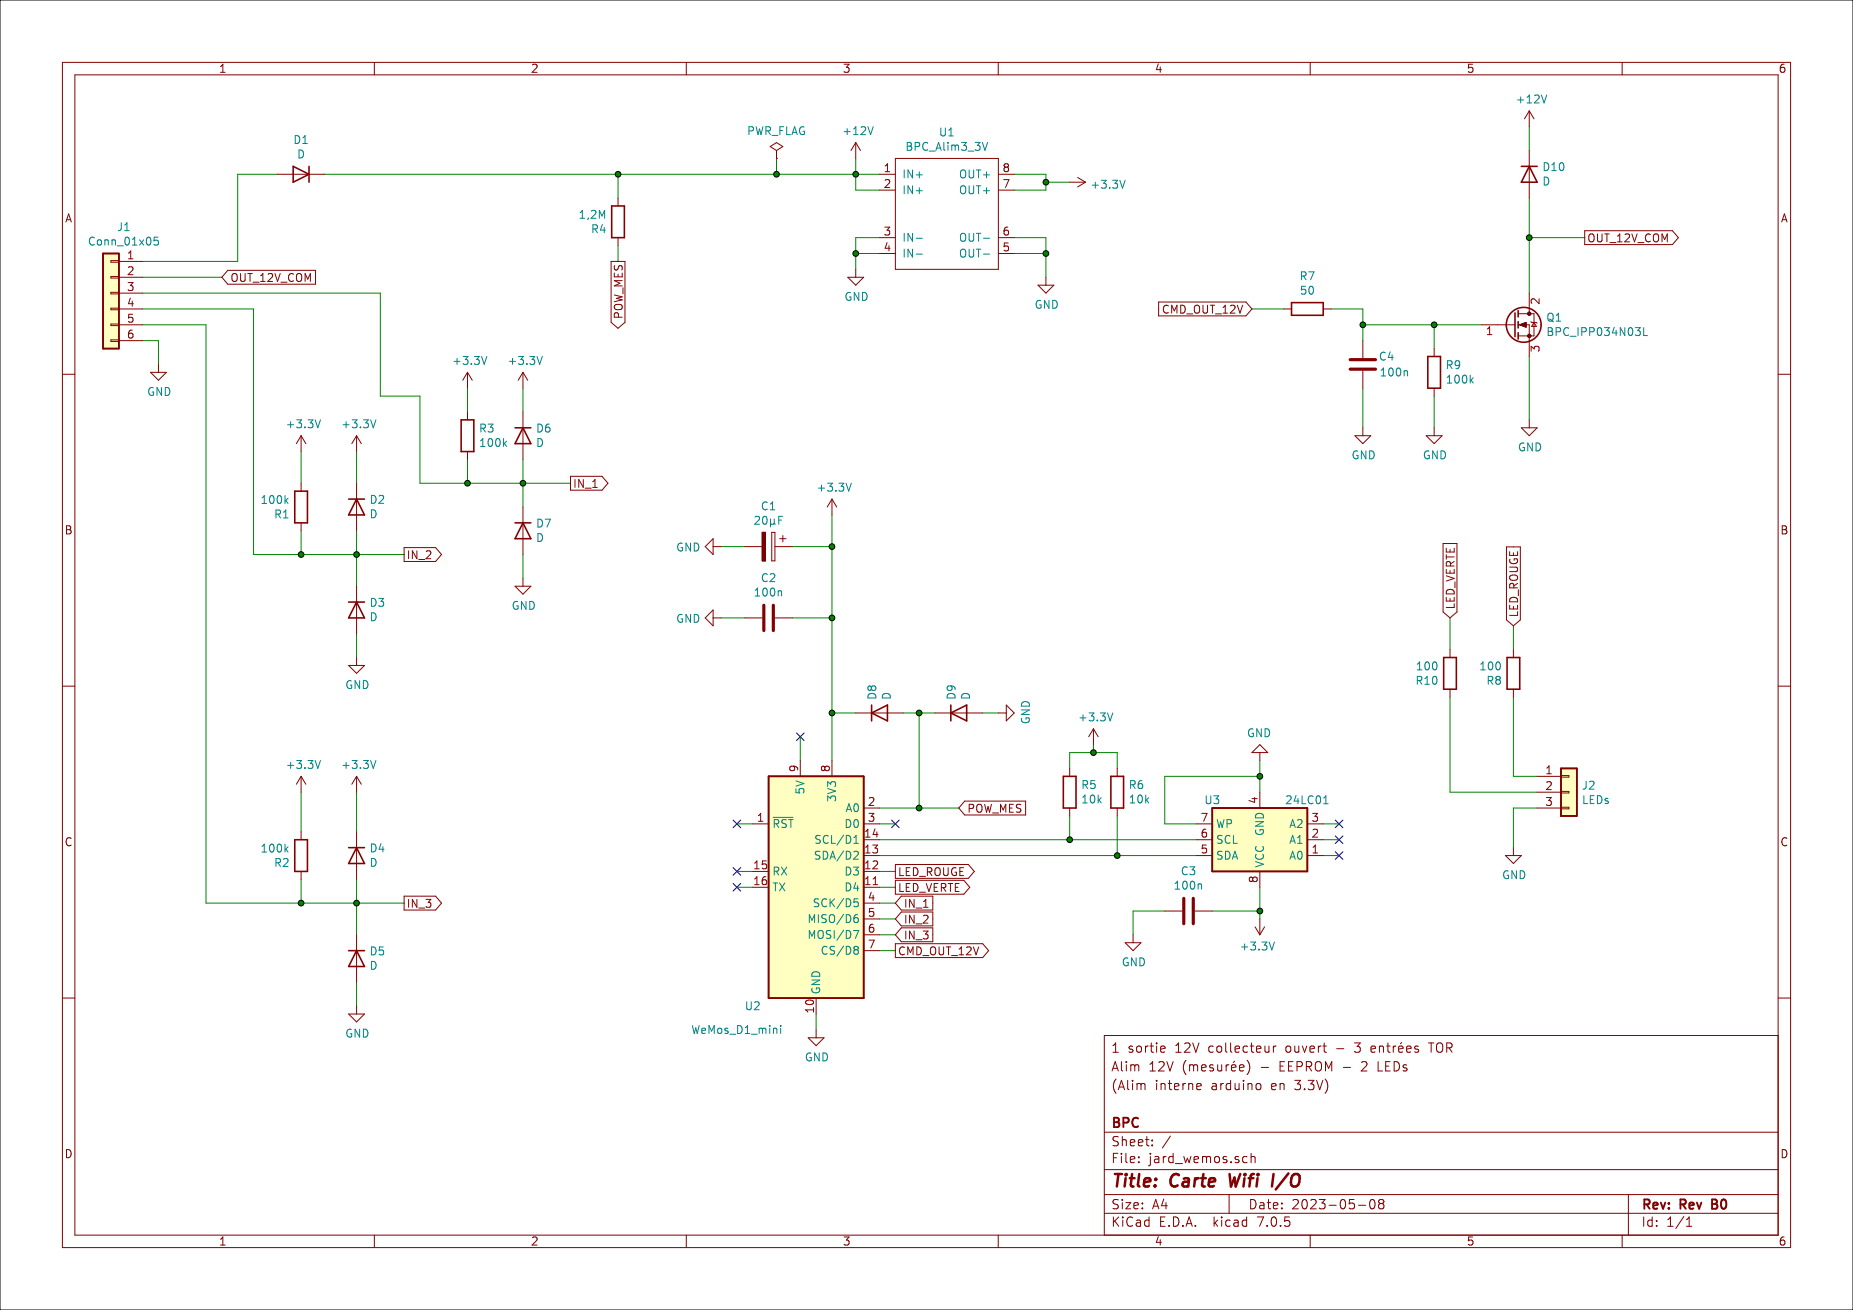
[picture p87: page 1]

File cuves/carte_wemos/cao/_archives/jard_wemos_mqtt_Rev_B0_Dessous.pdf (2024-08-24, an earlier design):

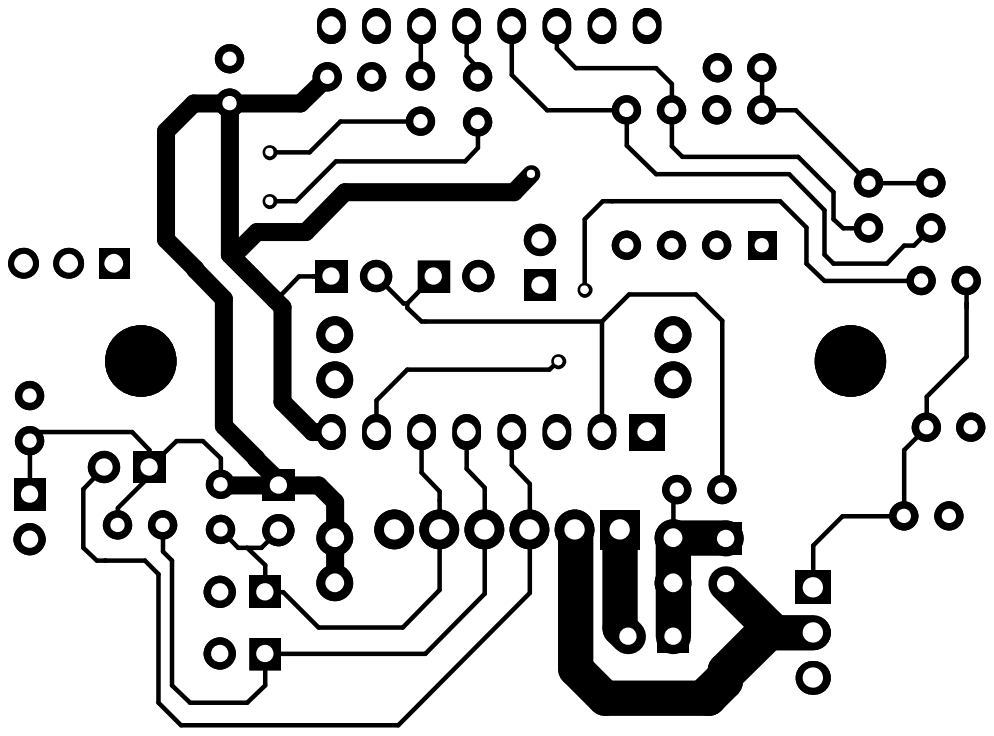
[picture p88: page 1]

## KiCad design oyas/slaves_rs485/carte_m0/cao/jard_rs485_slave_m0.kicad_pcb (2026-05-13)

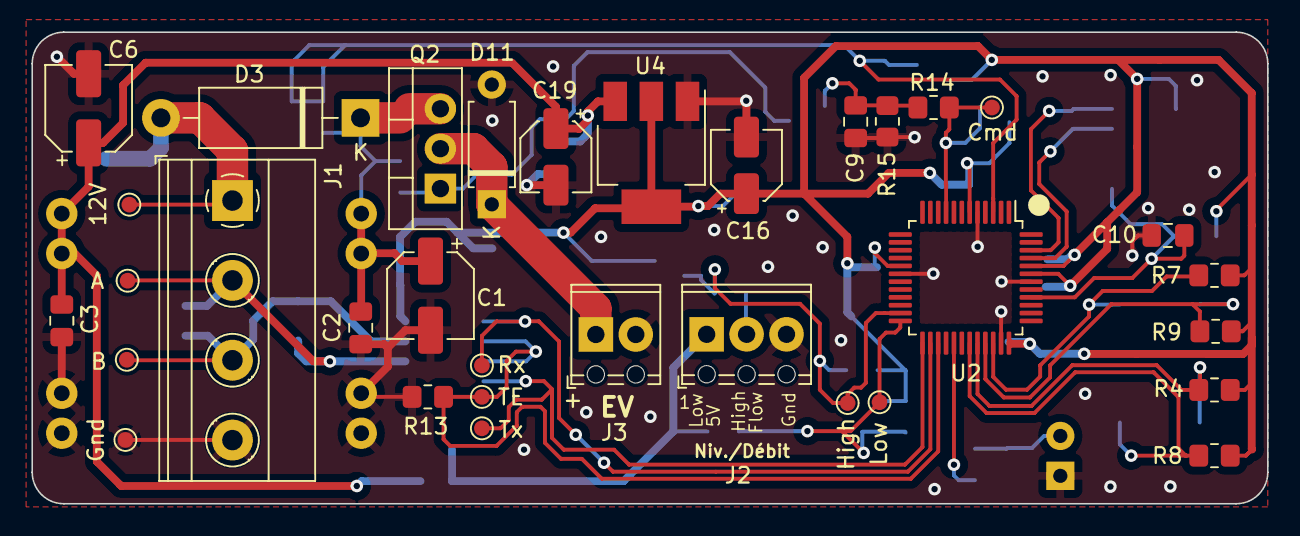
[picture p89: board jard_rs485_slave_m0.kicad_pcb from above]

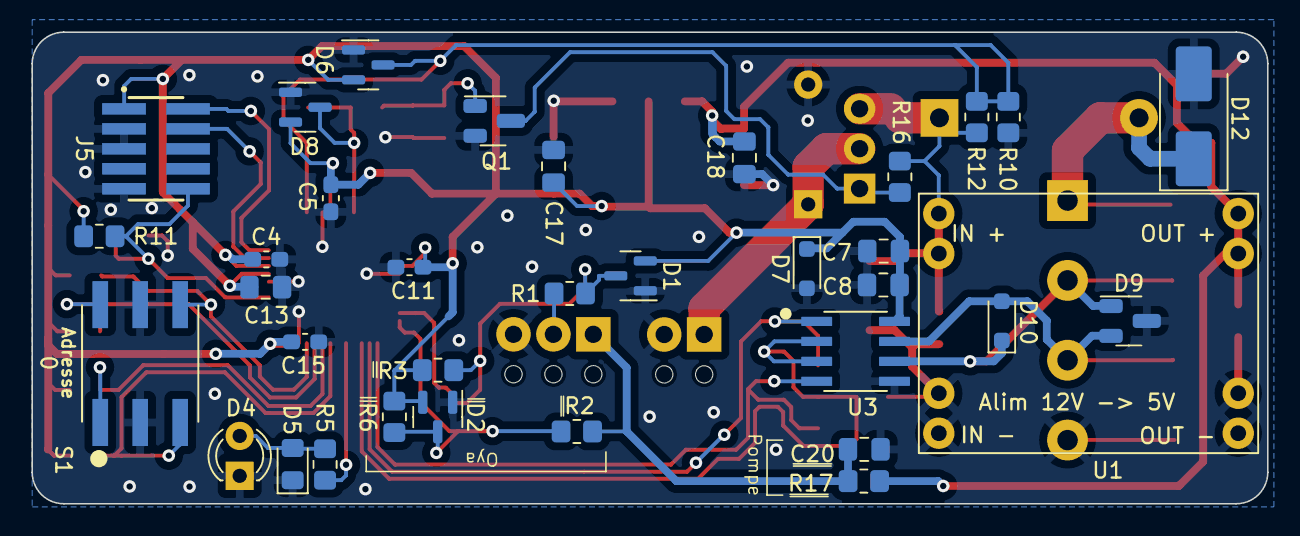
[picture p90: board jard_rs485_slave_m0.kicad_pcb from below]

Board: 2 copper layers, 78.6 x 30.0 mm, 68 parts (35 on the bottom side), 28 nets.

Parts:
C1: 33µF; CP_Elec_5x5.9
C2, C8, C9, C10, C17, C20: 100nF; C_0805_2012Metric_Pad1.18x1.45mm_HandSolder
C3, C18: 1nF; C_0805_2012Metric_Pad1.18x1.45mm_HandSolder
C4, C5, C11, C15: 100nF; C_0603_1608Metric_Pad1.08x0.95mm_HandSolder
C6: 10µF; CP_Elec_5x5.9
C7: 10µF; C_0805_2012Metric_Pad1.18x1.45mm_HandSolder
C13: 1µF; C_0805_2012Metric_Pad1.18x1.45mm_HandSolder
C16, C19: 10µF; CP_Elec_4x5.4
D1, D2, D6, D8: BAV99; SOT-23
D3: SR560; D_DO-15_P12.70mm_Horizontal
D4: LED; LED_D3.0mm_FlatTop
D5: LED; LED_0805_2012Metric_Pad1.15x1.40mm_HandSolder
D7, D10: SD12_SOD323; BPC_D_SOD-323_HandSoldering
D9: SM712_SOT23; BPC_SOT-23-3_HandSoldering
D11: 1N4007G; D_A-405_P7.62mm_Horizontal
D12: SMBJ18A; D_SMB_Handsoldering
J1: POWER; TerminalBlock_Phoenix_MKDS-1,5-4-5.08_1x04_P5.08mm_Horizont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
J2: Niveaux/Débit; TerminalBlock_Phoenix_MPT-0,5-3-2.54_1x03_P2.54mm_Horizontal
J3: EV1; TerminalBlock_Phoenix_MPT-0,5-2-2.54_1x02_P2.54mm_Horizontal
J5: BPC_PRG_FTSH-105-01-L-DV-K_1; BPC_SAMTEC_FTSH-105-01-L-DV-K
Q1: BPC_FMMT38C; BPC_SOT-23-3_HandSoldering
Q2: P03P4L-04; TO-220-3_Vertical
R1, R2, R14: 1k; R_0805_2012Metric_Pad1.20x1.40mm_HandSolder
R3, R4, R6, R7, R8, R9, R12, R13, R15, R16: 100k; R_0805_2012Metric_Pad1.20x1.40mm_HandSolder
R5: 220; R_0805_2012Metric_Pad1.20x1.40mm_HandSolder
R10: 27k; R_0805_2012Metric_Pad1.20x1.40mm_HandSolder
R11: 10k; R_0805_2012Metric_Pad1.20x1.40mm_HandSolder
R17: 0; R_0805_2012Metric_Pad1.20x1.40mm_HandSolder
S1: RDS-16S-74385-SMT; BPC_RDS-16S-74385-SMT
TP1: 12V; TestPoint_Pad_D1.0mm
TP2: Gnd; TestPoint_Pad_D1.0mm
TP3: High; TestPoint_Pad_D1.0mm
TP4: Low; TestPoint_Pad_D1.0mm
TP5: Rx; TestPoint_Pad_D1.0mm
TP6: Tx; TestPoint_Pad_D1.0mm
TP7: TE; TestPoint_Pad_D1.0mm
TP8: Cmd; TestPoint_Pad_D1.0mm
TP9: B; TestPoint_Pad_D1.0mm
TP10: A; TestPoint_Pad_D1.0mm
U1: BPC_Alim5V
U2: ATSAMD21G18A-A; TQFP-48_7x7mm_P0.5mm
U3: MAX3485; BPC_MAX485E_SOIC127P600X175-8N
U4: AP1117-15; BPC_SOT-223-3_TabPin2

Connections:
+3.3V: C4.1, C5.2, C7.1, C8.2, C11.2, C13.1, C15.1, C16.1, C17.1, D1.2 (A), D2.2 (A), D6.2 (A), D7.1 (A1), D8.2 (A), J5.01, R3.2, R4.2, R6.2, R7.2, R8.2, R9.2, R11.1, U2.6 (VDDANA), U2.17 (VDDIO), U2.36 (VDDIO), U2.43 (VDDCORE), U2.44 (VDDIN), U3.8 (VCC), U4.2 (VO)
+5V: C3.1, C6.1, C18.1, C19.1, R17.1, U1.7 (OUT+), U1.8 (OUT+), U4.3 (VI)
A1: R4.1, S1.1, U2.32 (PA23)
A2: R7.1, S1.2, U2.34 (PA25)
A3: R8.1, S1.4, U2.31 (PA22)
A4: R9.1, S1.8, U2.33 (PA24)
BUS_A: D9.1 (A1), D10.1 (A1), J1.2, TP10.1, U3.6 (A)
BUS_B: D9.2 (A2), D10.2 (A2), J1.3, TP9.1, U3.7 (B)
CMD_EV1: D8.3 (K), R14.1, TP8.1, U2.9 (PA04)
GND: C1.2, C2.2, C3.2, C4.2, C5.1, C6.2, C7.2, C8.1, C9.2, C10.1, C11.1, C13.2, C15.2, C16.2, C17.2, C18.2, C19.2, C20.1, D1.1 (K), D2.1 (K), D4.1 (K), D5.1 (K), D6.1 (K), D7.2 (A2), D8.1 (K), D9.3 (common), D11.2 (A), D12.2 (A2), J1.4, J2.3, J3.2, J5.03, J5.05, J5.09, Q1.2 (E), R10.1, R13.2, R15.2, S1.C_1 (C), S1.C_2 (C), TP2.1, U1.3 (IN-), U1.4 (IN-), U1.5 (OUT-), U1.6 (OUT-), U2.5 (GNDANA), U2.18 (GND), U2.35 (GND), U2.42 (GND), U3.5 (GND), U4.1 (GND)
LED: R5.1, U2.29 (PA20)
LVL_HIGH_FLOW: D1.3 (K), R1.2, R3.1, TP3.1, U2.23 (PA14)
LVL_LOW: D2.3 (K), R2.2, R6.1, TP4.1, U2.24 (PA15)
unnamed: D4.2 (A), D5.2 (A), R5.2
unnamed: D11.1 (K), J3.1, Q2.2 (D)
unnamed: D3.2 (A), D12.1 (A1), J1.1, TP1.1
unnamed: C20.2, J2.1, R2.1, R17.2
unnamed: J2.2, R1.1
unnamed: C9.1, Q1.1 (B), R14.2, R15.1
unnamed: Q1.3 (C), Q2.1 (G), R16.2
POWER_12V: C1.1, C2.1, D3.1 (K), Q2.3 (S), R12.2, R16.1, U1.1 (IN+), U1.2 (IN+)
POW_MES: D6.3 (K), R10.2, R12.1, U2.3 (PA02)
RX: TP5.1, U2.26 (PA17), U3.1 (RO)
SWCLK: J5.04, U2.45 (PA30)
SWDIO: J5.02, U2.46 (PA31)
TX: TP6.1, U2.25 (PA16), U3.4 (DI)
TX_EN: R13.1, TP7.1, U2.27 (PA18), U3.2 (~RE), U3.3 (DE)
/RESET: C10.2, J5.10, R11.2, U2.40 (~RESET)

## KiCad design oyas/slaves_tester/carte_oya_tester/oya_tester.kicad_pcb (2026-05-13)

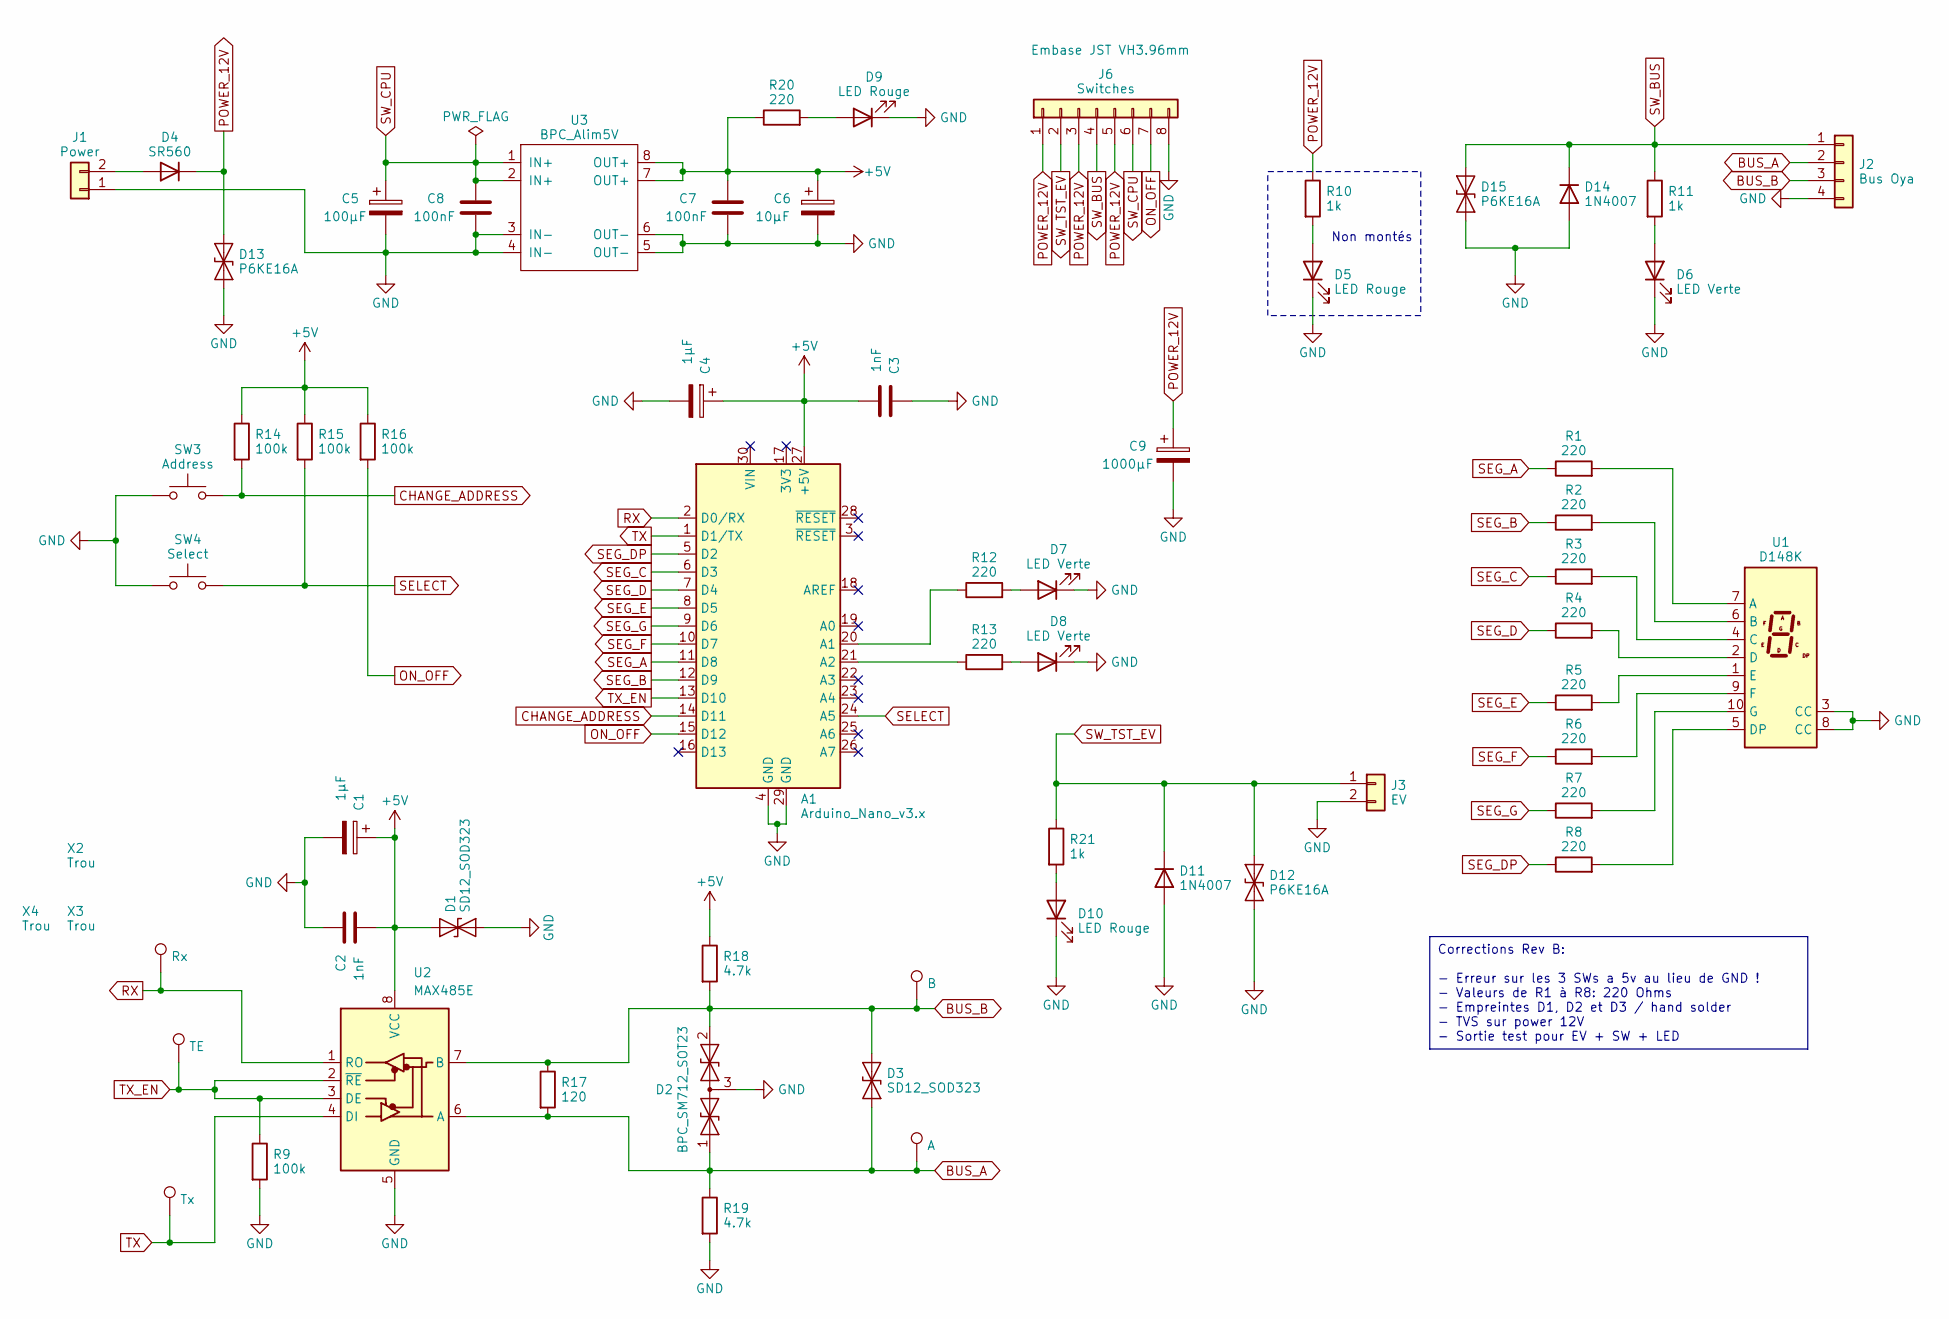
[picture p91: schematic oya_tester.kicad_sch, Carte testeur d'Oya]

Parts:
A1: Arduino_Nano_v3.x; BPC_Arduino_Nano
C1, C4: 1µF; C_0805_2012Metric_Pad1.18x1.45mm_HandSolder
C2, C3: 1nF; C_0805_2012Metric_Pad1.18x1.45mm_HandSolder
C5: 100µF; CP_Radial_D8.0mm_P3.50mm
C6: 10µF; CP_Radial_D5.0mm_P2.50mm
C7, C8: 100nF; C_0805_2012Metric_Pad1.18x1.45mm_HandSolder
C9: 1000µF; CP_Radial_D16.0mm_P7.50mm
D1, D3: SD12_SOD323; BPC_D_SOD-323_HandSoldering
D2: BPC_SM712_SOT23; BPC_SOT-23-3_HandSoldering
D4: SR560; D_DO-15_P12.70mm_Horizontal
D5, D9, D10: LED Rouge; LED_D3.0mm_FlatTop
D6, D7, D8: LED Verte; LED_D3.0mm_FlatTop
D11, D14: 1N4007; D_DO-41_SOD81_P3.81mm_Vertical_KathodeUp
D12, D15: P6KE16A; D_DO-15_P3.81mm_Vertical_KathodeUp
D13: P6KE16A; D_DO-15_P10.16mm_Horizontal
J1: Power; TerminalBlock_Phoenix_MKDS-1,5-2-5.08_1x02_P5.08mm_Horizont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
J2: Bus Oya; TerminalBlock_Phoenix_MKDS-1,5-4-5.08_1x04_P5.08mm_Horizont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
J3: EV; TerminalBlock_Phoenix_MKDS-1,5-2-5.08_1x02_P5.08mm_Horizont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
J6: Switches; JST_VH_B8P-VH-B_1x08_P3.96mm_Vertical
R1, R2, R3, R4, R5, R6, R7, R8, R12, R13, R20: 220; R_0805_2012Metric_Pad1.20x1.40mm_HandSolder
R9, R14, R15, R16: 100k; R_0805_2012Metric_Pad1.20x1.40mm_HandSolder
R10, R11, R21: 1k; R_0805_2012Metric_Pad1.20x1.40mm_HandSolder
R17: 120; R_Axial_DIN0204_L3.6mm_D1.6mm_P5.08mm_Horizontal
R18, R19: 4.7k; R_Axial_DIN0204_L3.6mm_D1.6mm_P5.08mm_Horizontal
SW3: Address; SW_PUSH_6mm
SW4: Select; SW_PUSH_6mm
TP1: Rx; TestPoint_Pad_D2.0mm
TP2: Tx; TestPoint_Pad_D2.0mm
TP3: TE; TestPoint_Pad_D2.0mm
TP4: B; TestPoint_Pad_D2.0mm
TP5: A; TestPoint_Pad_D2.0mm
U1: D148K; BPC_7SEG_D1X8K
U2: MAX485E; BPC_MAX485E_SOIC127P600X175-8N
U3: BPC_Alim5V
X2, X3, X4: Trou; BPC_Trou4mm_Fixation

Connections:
+5V: A1.27 (+5V), C1.1, C2.2, C3.2, C4.1, C6.1, C7.1, D1.1 (A1), R14.1, R15.1, R16.1, R18.1, R20.1, U2.8 (VCC), U3.7 (OUT+), U3.8 (OUT+)
BUS_A: D2.1 (A1), D3.1 (A1), J2.2, R17.2, R19.1, TP5.1, U2.6 (A)
BUS_B: D2.2 (A2), D3.2 (A2), J2.3, R17.1, R18.2, TP4.1, U2.7 (B)
CHANGE_ADDRESS: A1.14 (D11), R14.2, SW3.2
GND: A1.4 (GND), A1.29 (GND), C1.2, C2.1, C3.1, C4.2, C5.2, C6.2, C7.2, C8.2, C9.2, D1.2 (A2), D2.3 (common), D5.1 (K), D6.1 (K), D7.1 (K), D8.1 (K), D9.1 (K), D10.1 (K), D11.2 (A), D12.1 (A1), D13.1 (A1), D14.2 (A), D15.1 (A1), J1.1, J2.4, J3.2, J6.8, R9.2, R19.2, SW3.1, SW4.1, U1.3 (CC), U1.8 (CC), U2.5 (GND), U3.3 (IN-), U3.4 (IN-), U3.5 (OUT-), U3.6 (OUT-)
unnamed: A1.20 (A1), R12.1
unnamed: A1.21 (A2), R13.1
unnamed: D4.2 (A), J1.2
unnamed: D5.2 (A), R10.2
unnamed: D6.2 (A), R11.2
unnamed: D7.2 (A), R12.2
unnamed: D8.2 (A), R13.2
unnamed: D9.2 (A), R20.2
unnamed: D10.2 (A), R21.2
unnamed: R1.2, U1.7 (A)
unnamed: R2.2, U1.6 (B)
unnamed: R3.2, U1.4 (C)
unnamed: R4.2, U1.2 (D)
unnamed: R8.2, U1.5 (DP)
unnamed: R5.2, U1.1 (E)
unnamed: R6.2, U1.9 (F)
unnamed: R7.2, U1.10 (G)
ON_OFF: A1.15 (D12), J6.7, R16.2
POWER_12V: C9.1, D4.1 (K), D13.2 (A2), J6.1, J6.3, J6.5, R10.1
RX: A1.2 (D0/RX), TP1.1, U2.1 (RO)
SEG_A: A1.11 (D8), R1.1
SEG_B: A1.12 (D9), R2.1
SEG_C: A1.6 (D3), R3.1
SEG_D: A1.7 (D4), R4.1
SEG_DP: A1.5 (D2), R8.1
SEG_E: A1.8 (D5), R5.1
SEG_F: A1.10 (D7), R6.1
SEG_G: A1.9 (D6), R7.1
SELECT: A1.24 (A5), R15.2, SW4.2
SW_BUS: D14.1 (K), D15.2 (A2), J2.1, J6.4, R11.1
SW_CPU: C5.1, C8.1, J6.6, U3.1 (IN+), U3.2 (IN+)
SW_TST_EV: D11.1 (K), D12.2 (A2), J3.1, J6.2, R21.1
TX: A1.1 (D1/TX), TP2.1, U2.4 (DI)
TX_EN: A1.13 (D10), R9.1, TP3.1, U2.2 (~RE), U2.3 (DE)

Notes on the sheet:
Corrections Rev B: - Erreur sur les 3 SWs a 5v au lieu de GND ! - Valeurs de R1 à R8: 220 Ohms - Empreintes D1, D2 et D3 / hand solder - TVS sur power 12V - Sortie test pour EV + SW + LED
Non montés

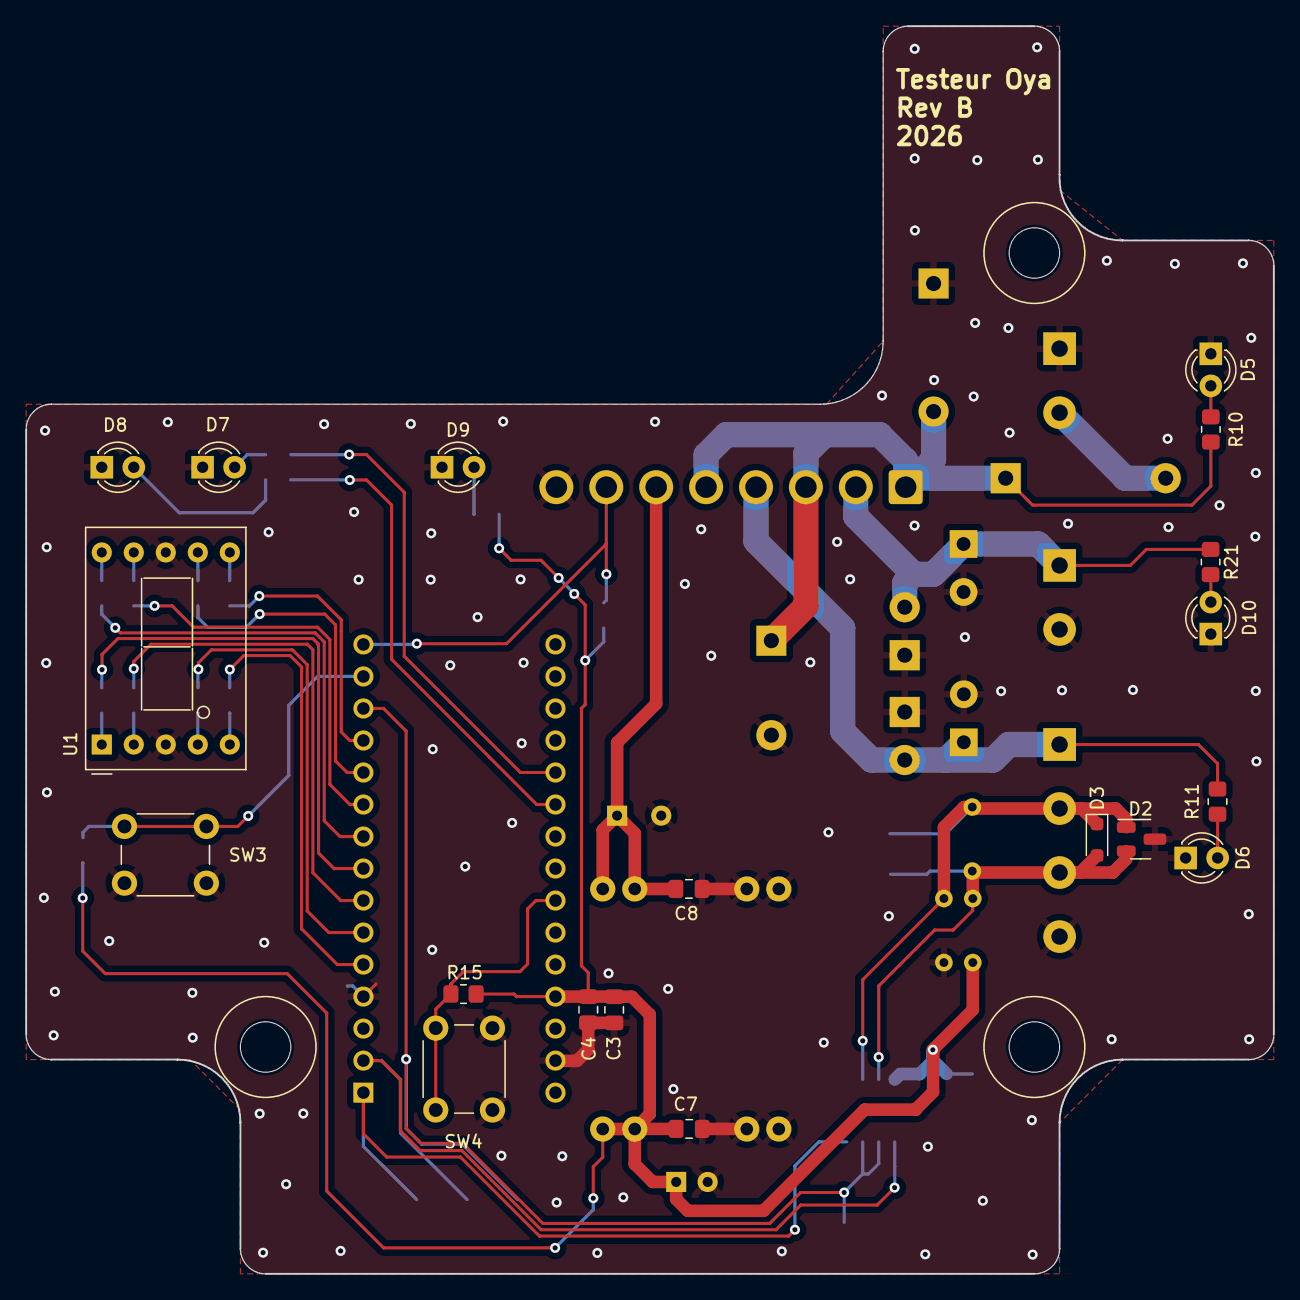
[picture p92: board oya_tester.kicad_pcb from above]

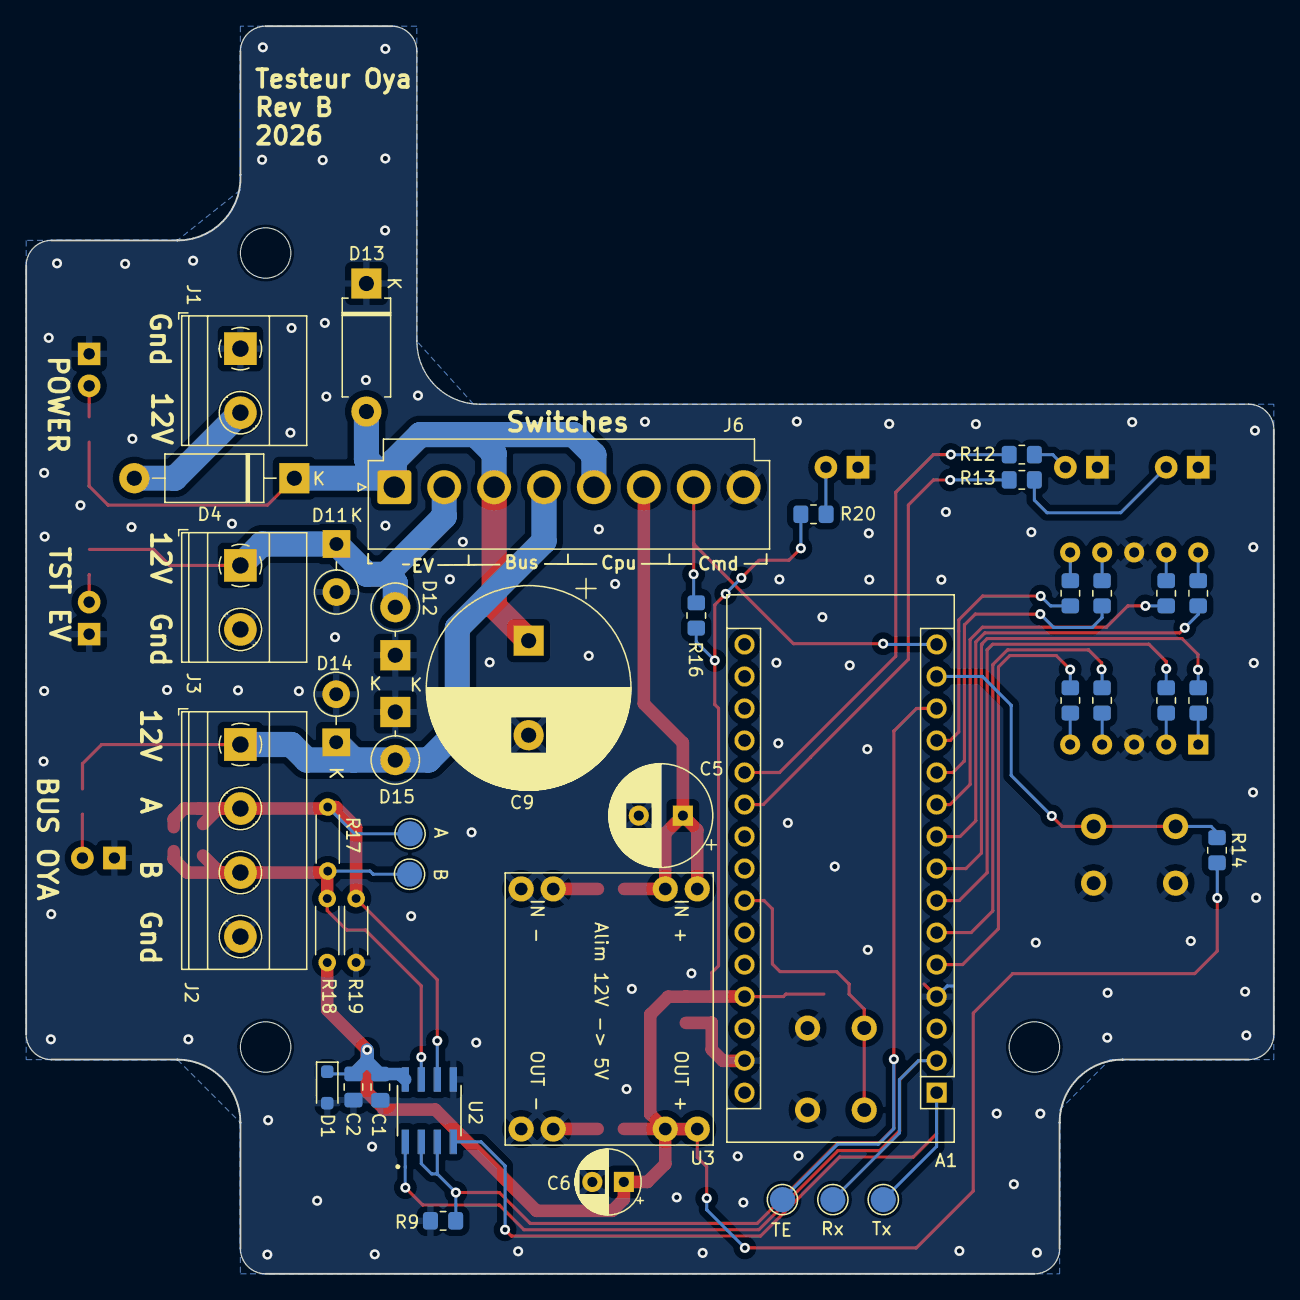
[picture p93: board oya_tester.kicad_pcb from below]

Board: 2 copper layers, 99.0 x 99.0 mm, 63 parts (41 on the bottom side), 39 nets.

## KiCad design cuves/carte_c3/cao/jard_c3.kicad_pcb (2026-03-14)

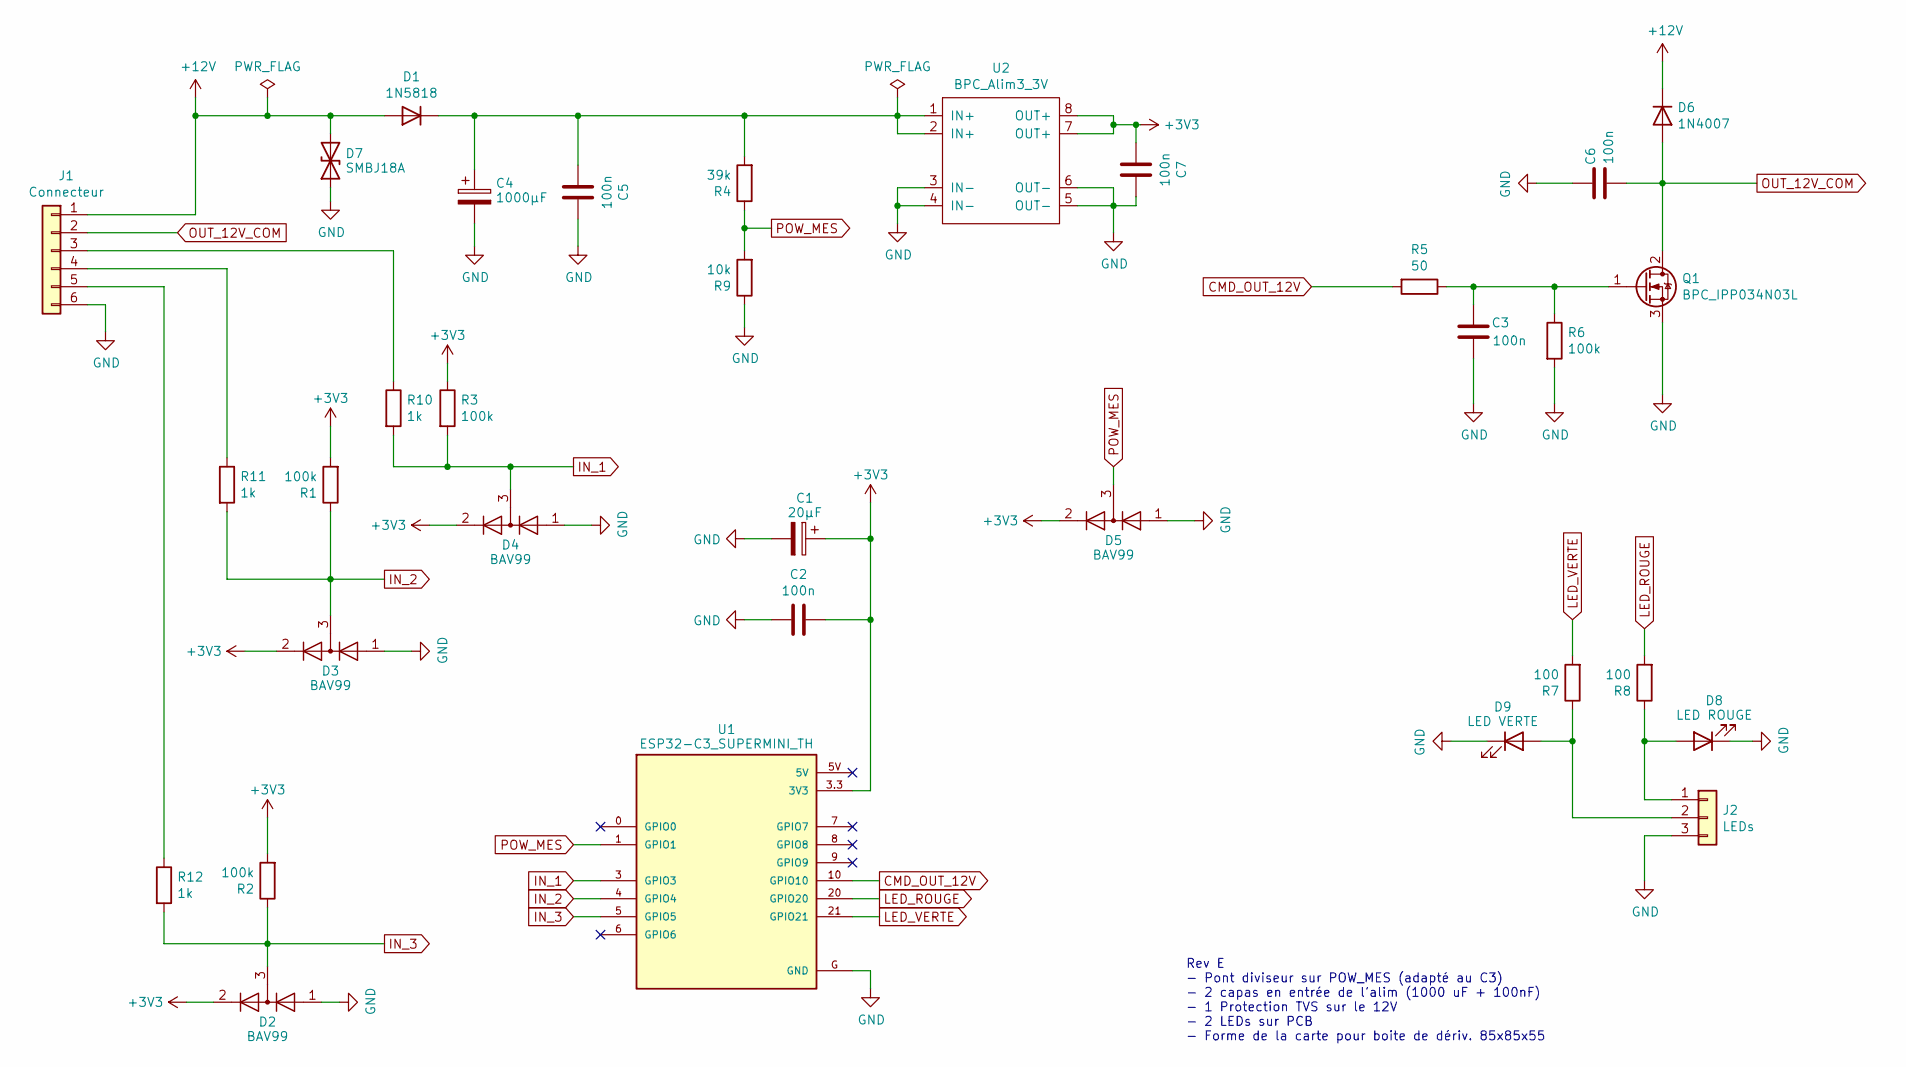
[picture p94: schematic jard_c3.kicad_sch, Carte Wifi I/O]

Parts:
C1: 20µF; C_Radial_D6.3mm_H7.0mm_P2.50mm
C2, C3, C5, C6, C7: 100n; C_0805_2012Metric_Pad1.18x1.45mm_HandSolder
C4: 1000µF; C_Radial_D16.0mm_H25.0mm_P7.50mm
D1: 1N5818; D_DO-41_SOD81_P10.16mm_Horizontal
D2, D3, D4, D5: BAV99; BPC_SOT-23-3_HandSoldering
D6: 1N4007; D_A-405_P2.54mm_Vertical_KathodeUp
D7: SMBJ18A; D_SMB_Handsoldering
D8: LED ROUGE; LED_D3.0mm
D9: LED VERTE; LED_D3.0mm
J1: Connecteur; TerminalBlock_Phoenix_MPT-0,5-6-2.54_1x06_P2.54mm_Horizontal
J2: LEDs; PinHeader_1x03_P2.54mm_Vertical
Q1: BPC_IPP034N03L; TO-220-3_Vertical
R1, R2, R3, R6: 100k; R_0805_2012Metric_Pad1.20x1.40mm_HandSolder
R4: 39k; R_0805_2012Metric_Pad1.20x1.40mm_HandSolder
R5: 50; R_0805_2012Metric_Pad1.20x1.40mm_HandSolder
R7, R8: 100; R_0805_2012Metric_Pad1.20x1.40mm_HandSolder
R9: 10k; R_0805_2012Metric_Pad1.20x1.40mm_HandSolder
R10, R11, R12: 1k; R_0805_2012Metric_Pad1.20x1.40mm_HandSolder
U1: ESP32-C3_SUPERMINI_TH; BPC_ESP32-C3_SUPERMINI
U2: BPC_Alim3_3V

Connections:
+3V3: C1.1, C2.1, C7.2, D2.2 (A), D3.2 (A), D4.2 (A), D5.2 (A), R1.2, R2.2, R3.1, U1.3.3 (3V3), U2.7 (OUT+), U2.8 (OUT+)
+12V: D1.2 (A), D6.1 (K), D7.2 (A2), J1.1
CMD_OUT_12V: R5.2, U1.10 (GPIO10)
GND: C1.2, C2.2, C3.2, C4.2, C5.1, C6.1, C7.1, D2.1 (K), D3.1 (K), D4.1 (K), D5.1 (K), D7.1 (A1), D8.1 (K), D9.1 (K), J1.6, J2.3, Q1.3 (S), R6.2, R9.1, U1.G (GND), U2.3 (IN-), U2.4 (IN-), U2.5 (OUT-), U2.6 (OUT-)
IN_1: D4.3 (K), R3.2, R10.2, U1.3 (GPIO3)
IN_2: D3.3 (K), R1.1, R11.2, U1.4 (GPIO4)
IN_3: D2.3 (K), R2.1, R12.2, U1.5 (GPIO5)
LED_ROUGE: R8.2, U1.20 (GPIO20)
LED_VERTE: R7.2, U1.21 (GPIO21)
unnamed: C4.1, C5.2, D1.1 (K), R4.2, U2.1 (IN+), U2.2 (IN+)
unnamed: D8.2 (A), J2.1, R8.1
unnamed: D9.2 (A), J2.2, R7.1
unnamed: J1.3, R10.1
unnamed: J1.4, R11.1
unnamed: J1.5, R12.1
unnamed: C3.1, Q1.1 (G), R5.1, R6.1
OUT_12V_COM: C6.2, D6.2 (A), J1.2, Q1.2 (D)
POW_MES: D5.3 (K), R4.1, R9.2, U1.1 (GPIO1)

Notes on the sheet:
Rev E - Pont diviseur sur POW_MES (adapté au C3) - 2 capas en entrée de l'alim (1000 uF + 100nF) - 1 Protection TVS sur le 12V - 2 LEDs sur PCB - Forme de la carte pour boite de dériv. 85x85x55

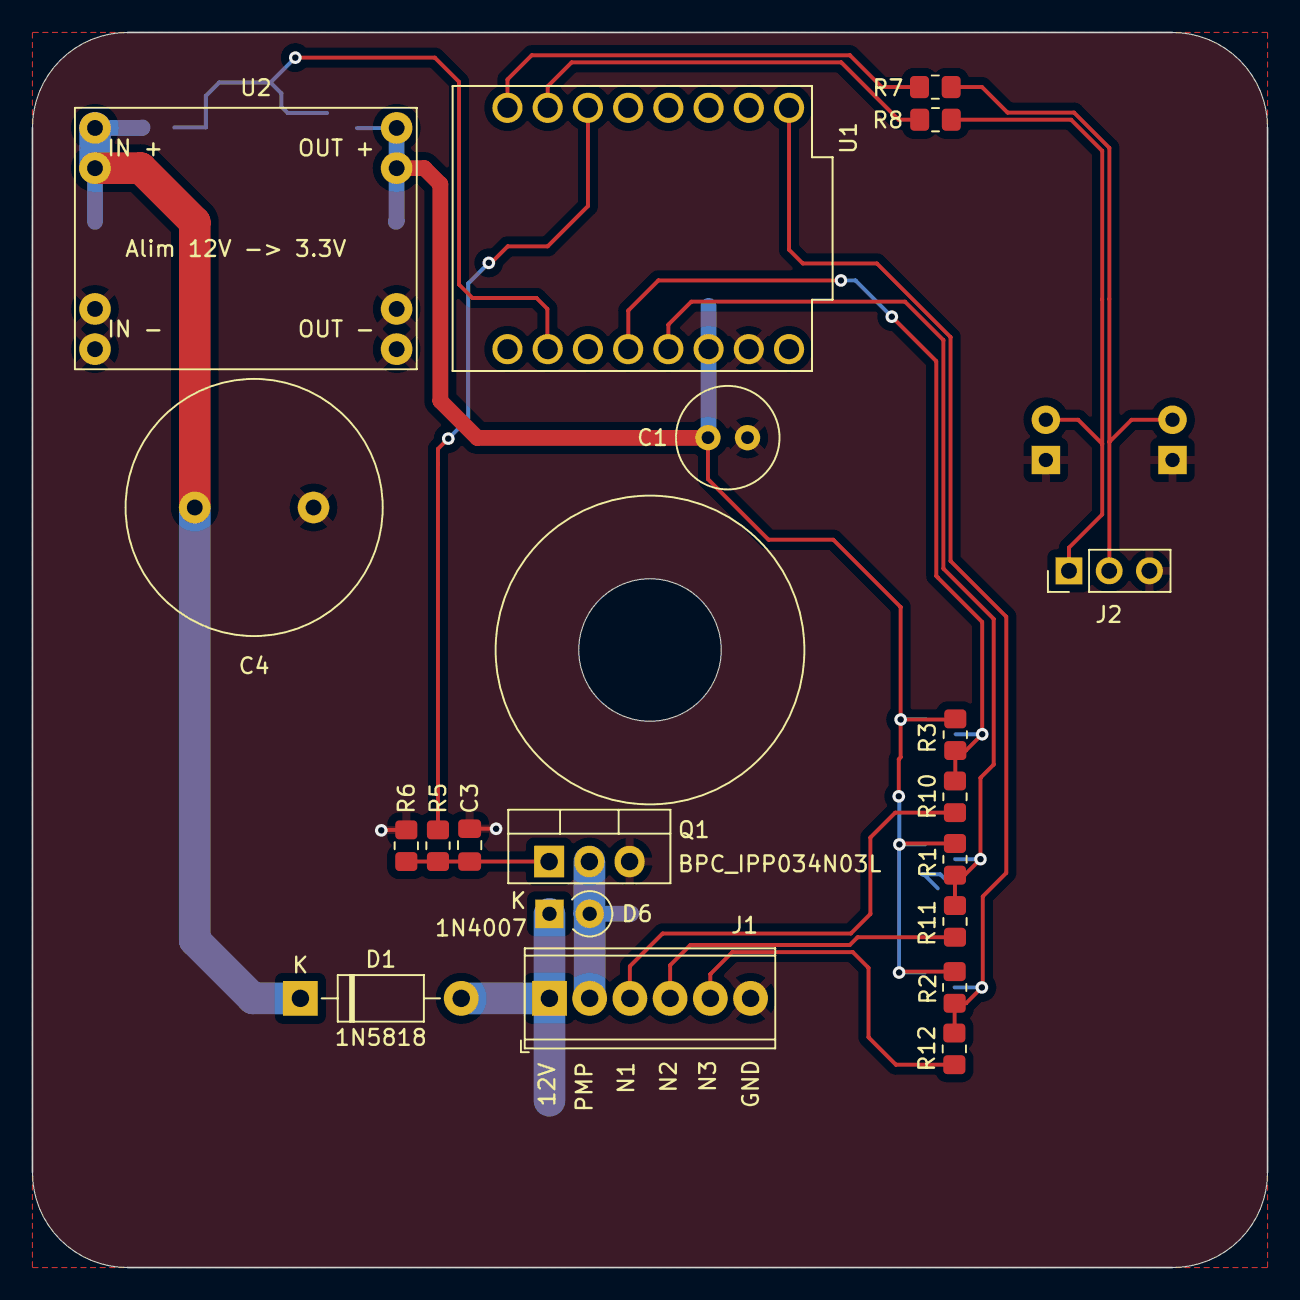
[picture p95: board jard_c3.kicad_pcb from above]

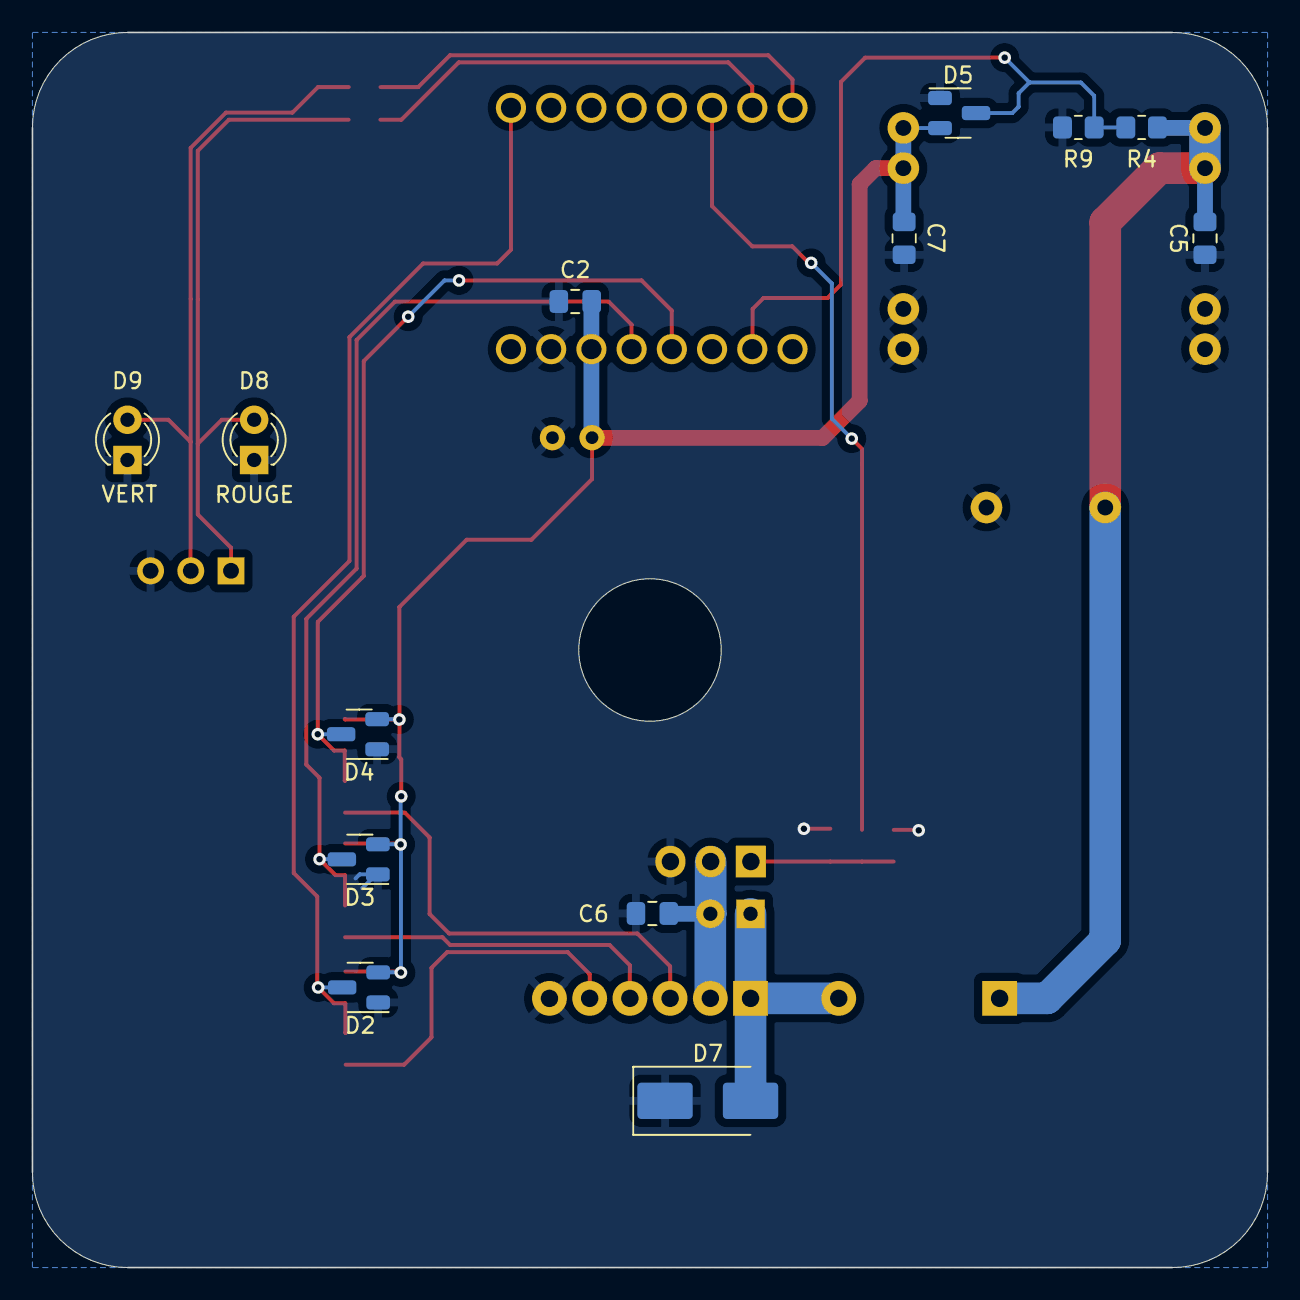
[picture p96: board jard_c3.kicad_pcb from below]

Board: 2 copper layers, 78.0 x 78.0 mm, 33 parts (13 on the bottom side), 18 nets.

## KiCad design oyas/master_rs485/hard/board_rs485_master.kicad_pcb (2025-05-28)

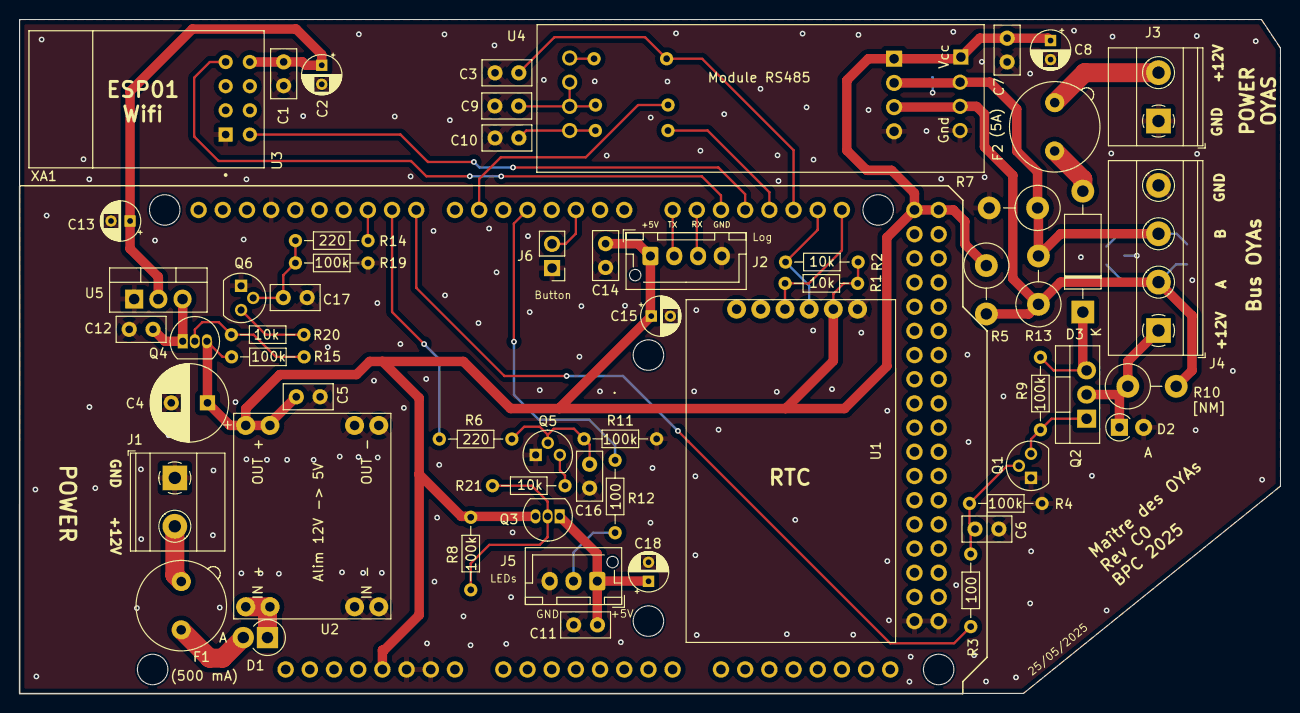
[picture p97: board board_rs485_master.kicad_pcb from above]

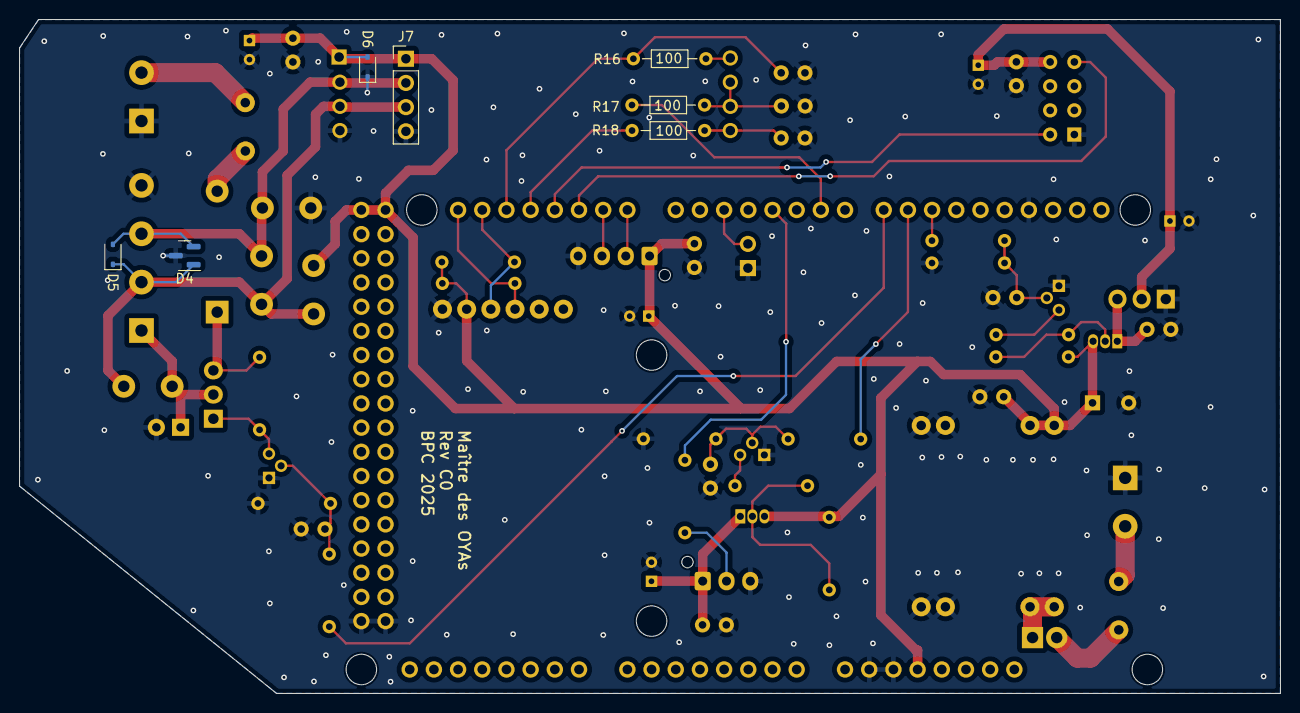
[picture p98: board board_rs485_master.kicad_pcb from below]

Board: 2 copper layers, 132.4 x 70.8 mm, 66 parts (7 on the bottom side), 40 nets.

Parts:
C1, C5, C6, C7, C11, C12, C14, C16, C17: 100nF; C_Disc_D5.0mm_W2.5mm_P2.50mm
C2, C8, C13, C15, C18: 10µF; CP_Radial_D4.0mm_P2.00mm
C3, C9, C10: 1nF; C_Disc_D5.0mm_W2.5mm_P2.50mm
C4: 100µF; CP_Radial_D8.0mm_P3.80mm
D1: SR560; D_DO-15_P2.54mm_Vertical_AnodeUp
D2: BAT42; D_A-405_P2.54mm_Vertical_AnodeUp
D3: SR560; D_DO-15_P12.70mm_Horizontal
D4: SM712_SOT23; SOT-23
D5, D6: SD12_SOD323; D_SOD-323
F1: 500 mA; Fuseholder_TR5_Littelfuse_No560_No460
F2: 5A; Fuseholder_TR5_Littelfuse_No560_No460
J1: POWER_12V; TerminalBlock_Phoenix_MKDS-1,5-2-5.08_1x02_P5.08mm_Horizont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
J2: Log; JST_XH_B4B-XH-AM_1x04_P2.50mm_Vertical
J3: POWER_OYAS_12V; TerminalBlock_Phoenix_MKDS-1,5-2-5.08_1x02_P5.08mm_Horizont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
J4: BUS_OYAS; TerminalBlock_Phoenix_MKDS-1,5-4-5.08_1x04_P5.08mm_Horizont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
J5: Leds RGB; JST_XH_B3B-XH-AM_1x03_P2.50mm_Vertical
J6: Button; PinHeader_1x02_P2.54mm_Vertical
J7: Adapt BUS; PinHeader_1x04_P2.54mm_Vertical
Q1, Q5, Q6: BPC_2N2222A; TO-92
Q2: P03P4L-04; TO-220-3_Vertical
Q3, Q4: BC327; TO-92_Inline
R1, R2, R20, R21: 10k; R_Axial_DIN0204_L3.6mm_D1.6mm_P7.62mm_Horizontal
R3, R12, R16, R17, R18: 100; R_Axial_DIN0204_L3.6mm_D1.6mm_P7.62mm_Horizontal
R4, R8, R9, R11, R15, R19: 100k; R_Axial_DIN0204_L3.6mm_D1.6mm_P7.62mm_Horizontal
R5, R7: 220; R_Axial_DIN0414_L11.9mm_D4.5mm_P5.08mm_Vertical
R6, R14: 220; R_Axial_DIN0204_L3.6mm_D1.6mm_P7.62mm_Horizontal
R10: R; R_Axial_DIN0414_L11.9mm_D4.5mm_P5.08mm_Vertical
R13: 128; R_Axial_DIN0414_L11.9mm_D4.5mm_P5.08mm_Vertical
U1: RtcArduino; BPC_RtcArduino
U2: BPC_Alim5V
U3: BPC_ESP8266-01_ESP-01; BPC_XCVR_ESP8266-01_ESP-01
U4: BPC_Mod485
U5: LM1117DT-3.3; TO-220-3_Vertical
XA1: Arduino_Mega2560_Shield; BPC_Arduino_Mega2560_Shield

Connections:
+5V: C4.1, C5.1, C7.1, C8.1, C14.1, C15.1, D6.2 (A2), J2.1, J7.1, Q3.3 (E), Q4.3 (E), R1.1, R2.1, R5.1, R8.1, R15.1, U1.2 (VCC), U2.7 (OUT+), U2.8 (OUT+), U4.1 (Vcc), XA1.5V1 (5V), XA1.5V3 (5V), XA1.5V4 (5V)
A: D4.1 (A1), D5.1 (A1), J4.2, J7.3, R5.2, R10.2, R13.1, U4.3 (A)
B: D4.2 (A2), D5.2 (A2), J4.3, J7.2, R7.1, R13.2, U4.2 (B)
CMD_LEDS_PWR: R6.1, XA1.D9
CMD_OYAS_PWR: R3.2, XA1.D8
CMD_WIFI_PWR: R14.1, XA1.D10
DATA_LEDS: R12.1, XA1.D4
GND: C1.2, C2.2, C3.2, C4.2, C5.2, C6.2, C7.2, C8.2, C9.2, C10.2, C11.2, C12.2, C13.2, C14.2, C15.2, C16.2, C17.2, C18.2, D2.2 (A), D4.3 (common), D6.1 (A1), J1.1, J2.4, J3.1, J4.4, J5.3, J6.1, J7.4, Q1.1, Q5.1, Q6.1, R4.2, R7.2, R11.2, R19.2, U1.1 (GND), U2.3 (IN-), U2.4 (IN-), U2.5 (OUT-), U2.6 (OUT-), U3.1 (GND), U4.4 (Gnd), U5.1 (GND), XA1.GND1 (GND), XA1.GND2 (GND), XA1.GND3 (GND), XA1.GND5 (GND), XA1.GND6 (GND)
unnamed: C6.1, Q1.2, R3.1, R4.1
unnamed: C16.1, Q5.2, R6.2, R11.1
unnamed: C17.1, Q6.2, R14.2, R19.1
unnamed: D1.2 (A), F1.1
unnamed: D1.1 (K), U2.1 (IN+), U2.2 (IN+)
unnamed: D2.1 (K), J4.1, Q2.2 (D), R10.1
unnamed: D3.2 (A), F2.1
unnamed: D3.1 (K), Q2.3 (S), R9.1
unnamed: F1.2, J1.2
unnamed: F2.2, J3.2
unnamed: C11.1, C18.1, J5.1, Q3.1 (C)
unnamed: J5.2, R12.2
unnamed: Q1.3, Q2.1 (G), R9.2
unnamed: Q3.2 (B), R8.2, R21.2
unnamed: Q4.2 (B), R15.2, R20.2
unnamed: C12.1, Q4.1 (C), U5.3 (VI)
unnamed: Q5.3, R21.1
unnamed: Q6.3, R20.1
unnamed: C9.1, R17.1, U4.6 (DE), U4.7 (RE)
unnamed: C10.1, R18.1, U4.5 (DI)
unnamed: R16.1, U4.8 (RO)
POWER_3.3: C1.1, C2.1, C13.1, U3.8 (VCC), U5.2 (VO)
RS485_RX: C3.1, R16.2, XA1.D19 (D19_RX1)
RS485_TX: R18.2, XA1.D18 (D18_TX1)
RX_LOG: J2.3, XA1.D15 (D15_RX3)
RX_WIFI: U3.5 (TXD), XA1.D17 (D17_RX2)
SCL: R1.2, U1.4 (SCL), XA1.D21 (D21_SCL)
SDA: R2.2, U1.3 (SDA), XA1.D20 (D20_SDA)
TEST_BTN: J6.2, XA1.D2 (D2_INT0)
TX_EN: R17.2, XA1.D6
TX_LOG: J2.2, XA1.D14 (D14_TX3)
TX_WIFI: U3.4 (RXD), XA1.D16 (D16_TX2)

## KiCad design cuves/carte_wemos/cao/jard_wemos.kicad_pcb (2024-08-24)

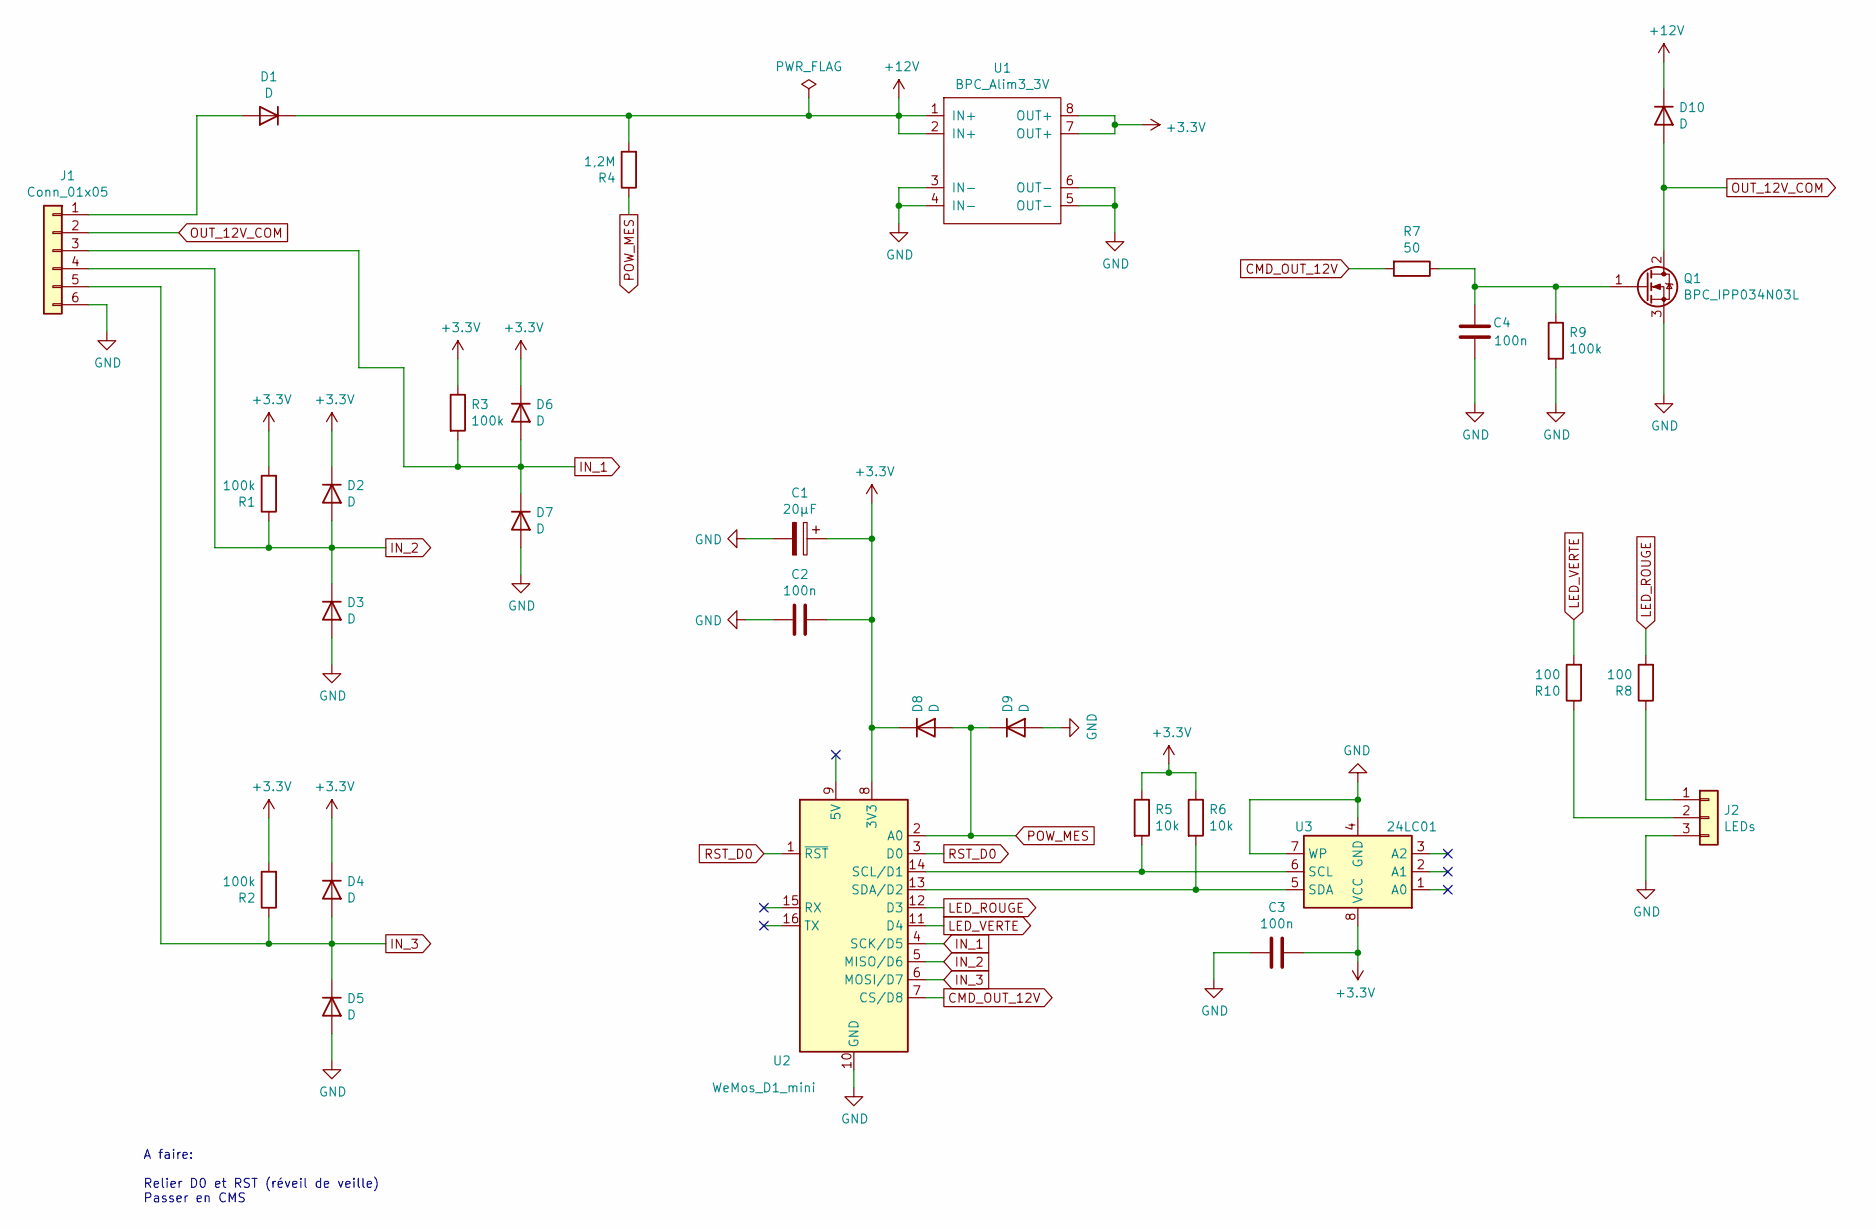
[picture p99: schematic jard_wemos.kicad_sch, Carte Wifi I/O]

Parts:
C1: 20µF; C_Radial_D6.3mm_H7.0mm_P2.50mm
C2, C3, C4: 100n; C_Disc_D3.0mm_W2.0mm_P2.50mm
D1, D2, D3, D4, D5, D6, D7, D8, D9, D10: D; D_A-405_P2.54mm_Vertical_KathodeUp
J1: Conn_01x05; TerminalBlock_Phoenix_MPT-0,5-6-2.54_1x06_P2.54mm_Horizontal
J2: LEDs; PinHeader_1x03_P2.54mm_Vertical
Q1: BPC_IPP034N03L; TO-220-3_Vertical
R1, R2, R3, R9: 100k; R_Axial_DIN0207_L6.3mm_D2.5mm_P2.54mm_Vertical
R4: 1,2M; R_Axial_DIN0207_L6.3mm_D2.5mm_P2.54mm_Vertical
R5, R6: 10k; R_Axial_DIN0207_L6.3mm_D2.5mm_P2.54mm_Vertical
R7: 50; R_Axial_DIN0207_L6.3mm_D2.5mm_P2.54mm_Vertical
R8, R10: 100; R_Axial_DIN0207_L6.3mm_D2.5mm_P2.54mm_Vertical
U1: BPC_Alim3_3V
U2: WeMos_D1_mini; WEMOS_D1_mini_light
U3: 24LC01; DIP-8_W7.62mm

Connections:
+3V3: C1.1, C2.1, C3.2, D2.1 (K), D4.1 (K), D6.1 (K), D8.1 (K), R1.2, R2.2, R3.1, R5.1, R6.1, U1.7 (OUT+), U1.8 (OUT+), U2.8 (3V3), U3.8 (VCC)
+12V: D1.1 (K), D10.1 (K), R4.2, U1.1 (IN+), U1.2 (IN+)
CMD_OUT_12V: R7.2, U2.7 (CS/D8)
GND: C1.2, C2.2, C3.1, C4.2, D3.2 (A), D5.2 (A), D7.2 (A), D9.2 (A), J1.6, J2.3, Q1.3 (S), R9.2, U1.3 (IN-), U1.4 (IN-), U1.5 (OUT-), U1.6 (OUT-), U2.10 (GND), U3.4 (GND), U3.7 (WP)
IN_1: D6.2 (A), D7.1 (K), J1.3, R3.2, U2.4 (SCK/D5)
IN_2: D2.2 (A), D3.1 (K), J1.4, R1.1, U2.5 (MISO/D6)
IN_3: D4.2 (A), D5.1 (K), J1.5, R2.1, U2.6 (MOSI/D7)
LED_ROUGE: R8.2, U2.12 (D3)
LED_VERTE: R10.2, U2.11 (D4)
unnamed: D1.2 (A), J1.1
unnamed: J2.1, R8.1
unnamed: J2.2, R10.1
unnamed: C4.1, Q1.1 (G), R7.1, R9.1
unnamed: R5.2, U2.14 (SCL/D1), U3.6 (SCL)
unnamed: R6.2, U2.13 (SDA/D2), U3.5 (SDA)
OUT_12V_COM: D10.2 (A), J1.2, Q1.2 (D)
POW_MES: D8.2 (A), D9.1 (K), R4.1, U2.2 (A0)
RST_D0: U2.1 (~RST), U2.3 (D0)

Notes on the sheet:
A faire: Relier D0 et RST (réveil de veille) Passer en CMS

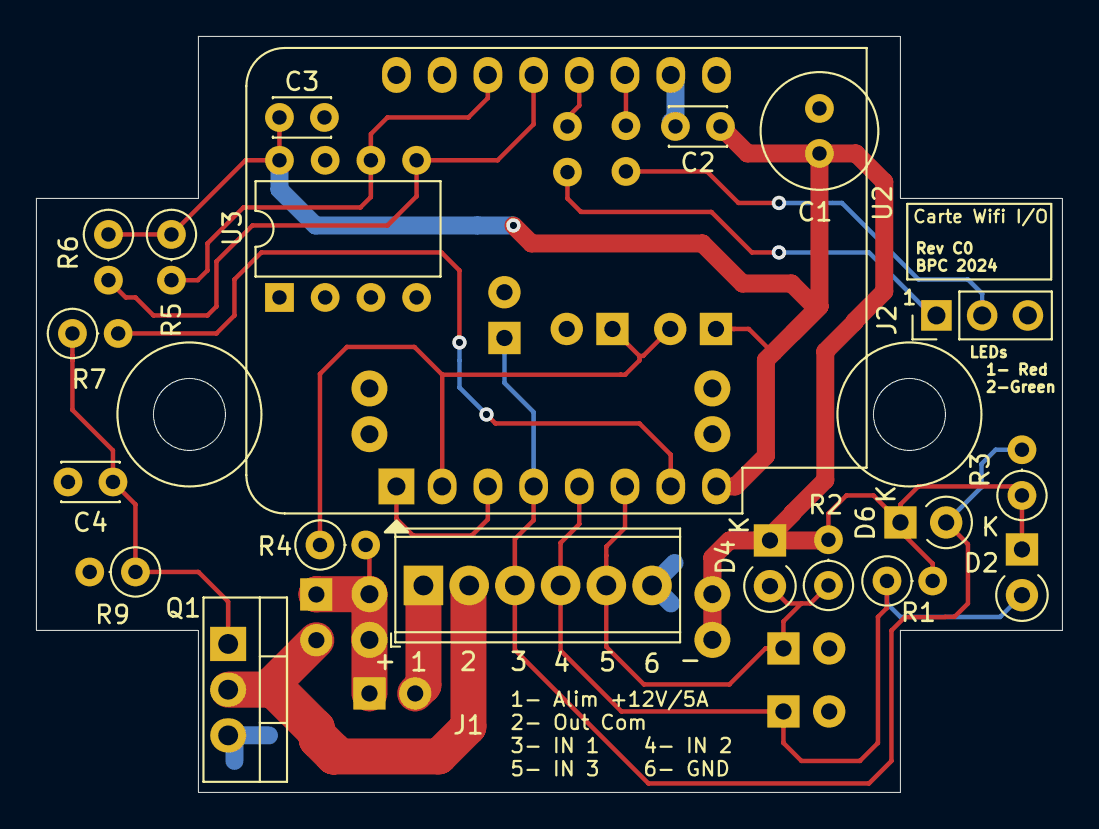
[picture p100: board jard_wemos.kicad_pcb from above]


Board: 2 copper layers, 57.0 x 42.0 mm, 30 parts (10 on the bottom side), 18 nets.

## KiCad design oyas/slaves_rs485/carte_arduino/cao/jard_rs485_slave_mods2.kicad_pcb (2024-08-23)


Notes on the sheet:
Version H0: - Changement de face du MOS - Amélioration pistes - 0805 pour un découplage 10µF de MAX485 (+0603 pour 100nF) Version G0: - Remplacement module RS485 par MAX485E - Ajout d'un cavalier pour couper RX pendant la programation via USB Version F0: - Déplacement piste LED trop proche du bord 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
TODO: - Mettre une alim 5V plus puissante (Le régulateur Nano casse sur les pompes) - Passer les condensateurs 603 en 805 - Essayer d'élargir les plages sur les protections MAX485 (Hand solder ?)
Carte de commande d'un Oya Esclave RS485 (Avec Module Nano) Petite Carte


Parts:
A1: Arduino_Nano_v3.x; BPC_Arduino_Nano
C7: 100nF; C_0603_1608Metric
D1: LED; LED_0805_2012Metric_Pad1.15x1.40mm_HandSolder
D2: SR560; D_DO-15_P12.70mm_Horizontal
D3: LED; LED_D3.0mm_FlatTop
D5: BAV99; SOT-23
J1: POWER; TerminalBlock_Phoenix_MKDS-1,5-4-5.08_1x04_P5.08mm_Horizont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
R1: 40k; R_0805_2012Metric_Pad1.20x1.40mm_HandSolder
R2: 100k; R_0805_2012Metric_Pad1.20x1.40mm_HandSolder
R12: 220; R_0805_2012Metric_Pad1.20x1.40mm_HandSolder
S1: RDS-16S-74385-SMT; BPC_RDS-16S-74385-SMT; PARTREV 1.0
TP2, TP5: TestPoint; TestPoint_Pad_D1.5mm
U6: BPC_DHT22

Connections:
+5V: A1.27 (+5V), C7.1, D5.2 (A), U6.1 (VDD); also elsewhere on the board
A1: A1.23 (A4), S1.1
A2: A1.21 (A2), S1.2
A3: A1.24 (A5), S1.4
A4: A1.22 (A3), S1.8
CMD_EV1: A1.10 (D7); also elsewhere on the board
FLOW: A1.7 (D4); also elsewhere on the board
GND: A1.4 (GND), A1.29 (GND), C7.2, D1.1 (K), D3.1 (K), D5.1 (K), J1.4, R1.1, S1.C_1 (C), S1.C_2 (C), TP5.1, U6.4 (GND); also elsewhere on the board
LED: A1.11 (D8), R12.1
LVL_HIGH: A1.6 (D3); also elsewhere on the board
LVL_LOW: A1.5 (D2); also elsewhere on the board
unnamed: D1.2 (A), D3.2 (A), R12.2
unnamed: D2.2 (A), J1.1, TP2.1
POWER_12V: A1.30 (VIN), D2.1 (K), R2.2; also elsewhere on the board
POW_MES: A1.20 (A1), D5.3 (K), R1.2, R2.1
TEMP: A1.13 (D10), U6.2 (DATA)
TX: A1.1 (D1/TX); also elsewhere on the board
TX_EN: A1.9 (D6); also elsewhere on the board


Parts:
C1: 10µF; C_0805_2012Metric
C2, C6: 100nF; C_0603_1608Metric
D4, D11: SD12_SOD323; D_SOD-323
D6, D7, D8, D10: BAV99; SOT-23
D9: SM712_SOT23; SOT-23
D13: 1N4007G; D_A-405_P5.08mm_Vertical_KathodeUp
J3: Débit; TerminalBlock_Phoenix_MPT-0,5-3-2.54_1x03_P2.54mm_Horizontal
J4: Niveaux; TerminalBlock_Phoenix_MPT-0,5-3-2.54_1x03_P2.54mm_Horizontal
J6: EV1; TerminalBlock_Phoenix_MPT-0,5-2-2.54_1x02_P2.54mm_Horizontal
JP2: Prog; PinHeader_1x03_P2.54mm_Vertical
Q4: BPC_FMMT38C; BPC_SOT-23-3
Q6: P03P4L-04; TO-220-3_Vertical
R3, R15, R17: 100k; R_0805_2012Metric_Pad1.20x1.40mm_HandSolder
R7, R8, R9: 100; R_0805_2012Metric_Pad1.20x1.40mm_HandSolder
R13: 220; R_0805_2012Metric_Pad1.20x1.40mm_HandSolder
TP1, TP3, TP4, TP11, TP12, TP13, TP15: TestPoint; TestPoint_Pad_D1.5mm
U1: MAX485E; BPC_MAX485E_SOIC127P600X175-8N

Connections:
+5V: C1.1, C2.2, D4.1 (A1), D6.2 (A), D7.2 (A), D8.2 (A), D10.2 (A), J3.1, U1.8 (VCC); also elsewhere on the board
CMD_EV1: D10.3 (K), R13.1, TP15.1; also elsewhere on the board
FLOW: D8.3 (K), R7.2, TP11.1; also elsewhere on the board
GND: C1.2, C2.1, C6.2, D4.2 (A2), D6.1 (K), D7.1 (K), D8.1 (K), D9.3 (common), D10.1 (K), D13.2 (A), J3.3, J4.3, J6.2, Q4.2 (E), R3.2, R15.2, U1.5 (GND); also elsewhere on the board
LVL_HIGH: D6.3 (K), R8.2, TP12.1; also elsewhere on the board
LVL_LOW: D7.3 (K), R9.2, TP13.1; also elsewhere on the board
unnamed: D13.1 (K), J6.1, Q6.2 (D)
unnamed: J3.2, R7.1
unnamed: J4.1, R9.1
unnamed: J4.2, R8.1
unnamed: JP2.2 (C), U1.1 (RO)
unnamed: C6.1, Q4.1 (B), R13.2, R15.1
unnamed: Q4.3 (C), Q6.1 (G), R17.2
POWER_12V: Q6.3 (S), R17.1; also elsewhere on the board
TX: TP3.1, U1.4 (DI); also elsewhere on the board
TX_EN: R3.1, TP4.1, U1.2 (~RE), U1.3 (DE); also elsewhere on the board

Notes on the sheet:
Mesure de débit
Ou BC817-25
BUS RS485
Sortie cmd 12V
Niveaux

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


Board: 2 copper layers, 79.2 x 30.0 mm, 48 parts (27 on the bottom side), 28 nets.

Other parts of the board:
TP6, TP7: TestPoint; TestPoint_Pad_D1.5mm

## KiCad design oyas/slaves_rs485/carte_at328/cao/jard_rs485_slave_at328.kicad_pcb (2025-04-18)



Board: 2 copper layers, 77.6 x 30.0 mm, 60 parts (30 on the bottom side), 33 nets.

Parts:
C1: 10nF; C_0805_2012Metric_Pad1.18x1.45mm_HandSolder
C2, C3, C12, C13, C14, C15: 100nF; C_0805_2012Metric_Pad1.18x1.45mm_HandSolder
C5, C6: 6pF; C_0603_1608Metric_Pad1.08x0.95mm_HandSolder
C7, C9: 10µF; CP_Elec_5x5.9
C8, C10: 1nF; C_0805_2012Metric_Pad1.18x1.45mm_HandSolder
C11: 1nF; C_0805_2012Metric
D1, D2, D7, D10, D11: BAV99; SOT-23
D3, D5: SD12_SOD323; D_SOD-323
D4: SM712_SOT23; SOT-23
D6: SR560; D_DO-15_P12.70mm_Horizontal
D8: LED; LED_D3.0mm_FlatTop
D9: LED; LED_0805_2012Metric_Pad1.15x1.40mm_HandSolder
D12: 1N4007G; D_A-405_P5.08mm_Vertical_KathodeUp
J1: EV1; TerminalBlock_Phoenix_MPT-0,5-2-2.54_1x02_P2.54mm_Horizontal
J2: Niveaux; TerminalBlock_Phoenix_MPT-0,5-3-2.54_1x03_P2.54mm_Horizontal
J3: POWER; TerminalBlock_Phoenix_MKDS-1,5-4-5.08_1x04_P5.08mm_Horizont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
J4: Débit; TerminalBlock_Phoenix_MPT-0,5-3-2.54_1x03_P2.54mm_Horizontal
J5: ISCP; BPC_ISCP_CMS
Q1: BPC_FMMT38C; BPC_SOT-23-3
Q2: P03P4L-04; TO-220-3_Vertical
R1, R2, R7, R12: 100; R_0805_2012Metric_Pad1.20x1.40mm_HandSolder
R3, R5, R9, R10: 100k; R_0805_2012Metric_Pad1.20x1.40mm_HandSolder
R4: 40k; R_0805_2012Metric_Pad1.20x1.40mm_HandSolder
R6, R8: 220; R_0805_2012Metric_Pad1.20x1.40mm_HandSolder
S1: RDS-16S-74385-SMT; BPC_RDS-16S-74385-SMT
TP1: H; TestPoint_Pad_D2.0mm
TP2: L; TestPoint_Pad_D2.0mm
TP3: Rx; TestPoint_Pad_D2.0mm
TP4: Tx; TestPoint_Pad_D2.0mm
TP5: TE; TestPoint_Pad_D2.0mm
TP6: B; TestPoint_Pad_D2.0mm
TP7: A; TestPoint_Pad_D2.0mm
TP8: 12V; TestPoint_Pad_D2.0mm
TP9: Gnd; TestPoint_Pad_D2.0mm
TP10: F; TestPoint_Pad_D2.0mm
TP11: C; TestPoint_Pad_D2.0mm
U1: BPC_Alim5V
U2: ATmega328P-A; TQFP-32_7x7mm_P0.8mm
U3: MAX485E; BPC_MAX485E_SOIC127P600X175-8N
Y1: 8MHz; BPC_Quartz_8MHz

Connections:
+5V: C1.1, C2.2, C7.1, C8.1, C11.1, C12.1, C13.1, D1.2 (A), D2.2 (A), D3.1 (A1), D7.2 (A), D10.2 (A), D11.2 (A), J4.1, J5.2 (VCC), R12.2, U1.7 (OUT+), U1.8 (OUT+), U2.4 (VCC), U2.6 (VCC), U2.18 (AVCC), U3.8 (VCC)
A1: S1.1, U2.1 (PD3)
A2: S1.2, U2.10 (PD6)
A3: S1.4, U2.2 (PD4)
A4: S1.8, U2.9 (PD5)
BUS_A: D4.1 (A1), D5.1 (A1), J3.2, TP7.1, U3.6 (A)
BUS_B: D4.2 (A2), D5.2 (A2), J3.3, TP6.1, U3.7 (B)
CMD_EV1: D11.3 (K), R8.1, TP11.1, U2.11 (PD7)
FLOW: D10.3 (K), R7.2, TP10.1, U2.12 (PB0), U2.32 (PD2)
GND: C1.2, C2.1, C3.2, C5.2, C6.1, C7.2, C8.2, C9.2, C10.2, C11.2, C12.2, C13.2, C14.1, C15.2, D1.1 (K), D2.1 (K), D3.2 (A2), D4.3 (common), D7.1 (K), D8.1 (K), D9.1 (K), D10.1 (K), D11.1 (K), D12.2 (A), J1.2, J2.3, J3.4, J4.3, J5.6 (GND), Q1.2 (E), R3.2, R4.1, R9.2, S1.C_1 (C), S1.C_2 (C), TP9.1, U1.3 (IN-), U1.4 (IN-), U1.5 (OUT-), U1.6 (OUT-), U2.3 (GND), U2.5 (GND), U2.21 (GND), U3.5 (GND)
LED: R6.1, U2.27 (PC4)
LVL_HIGH: D1.3 (K), R1.2, TP1.1, U2.14 (PB2)
LVL_LOW: D2.3 (K), R2.2, TP2.1, U2.13 (PB1)
MISO: J5.1 (MISO), U2.16 (PB4)
MOSI: J5.4 (MOSI), U2.15 (PB3)
unnamed: D6.2 (A), J3.1, TP8.1
unnamed: D8.2 (A), D9.2 (A), R6.2
unnamed: D12.1 (K), J1.1, Q2.2 (D)
unnamed: J2.1, R2.1
unnamed: J2.2, R1.1
unnamed: J4.2, R7.1
unnamed: C3.1, Q1.1 (B), R8.2, R9.1
unnamed: Q1.3 (C), Q2.1 (G), R10.2
unnamed: C14.2, U2.20 (AREF)
unnamed: C6.2, U2.7 (XTAL1/PB6), Y1.2
unnamed: C5.1, U2.8 (XTAL2/PB7), Y1.1
POWER_12V: C9.1, C10.1, D6.1 (K), Q2.3 (S), R5.2, R10.1, U1.1 (IN+), U1.2 (IN+)
POW_MES: D7.3 (K), R4.2, R5.1, U2.25 (PC2)
RESET: C15.1, J5.5 (RST), R12.1, U2.29 (~RESET/PC6)
RX: TP3.1, U2.30 (PD0), U3.1 (RO)
SCK: J5.3 (SCK), U2.17 (PB5)
TX: TP4.1, U2.31 (PD1), U3.4 (DI)
TX_EN: R3.1, TP5.1, U2.28 (PC5), U3.2 (~RE), U3.3 (DE)

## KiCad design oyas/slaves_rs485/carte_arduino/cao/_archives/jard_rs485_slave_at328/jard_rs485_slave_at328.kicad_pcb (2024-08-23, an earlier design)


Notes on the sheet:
Carte de commande d'un Oya Esclave RS485 (Avec ATMEGA328)


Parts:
C5, C8, C13: 100nF; C_0603_1608Metric
C7, C9: 1nF; C_0603_1608Metric
D1: LED; LED_0805_2012Metric_Pad1.15x1.40mm_HandSolder
D3: LED; LED_D3.0mm_FlatTop
J7: ISCP; BPC_ISCP_CMS
R12: 220; R_0805_2012Metric_Pad1.20x1.40mm_HandSolder
R26: 1k; R_0805_2012Metric_Pad1.20x1.40mm_HandSolder
U5: ATmega328P-A; TQFP-32_7x7mm_P0.8mm
U6: BPC_DHT22
Y1: Resonator; BPC_16MHz_CSTNE16M0V530000R0; PARTREV JGC42-8853B

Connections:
+5V: C5.2, C7.1, C8.2, C9.2, J7.2 (VCC), R26.2, U5.4 (VCC), U5.6 (VCC), U5.18 (AVCC), U6.1 (VDD); also elsewhere on the board
A1: U5.27 (PC4); also elsewhere on the board
A2: U5.25 (PC2); also elsewhere on the board
A3: U5.28 (PC5); also elsewhere on the board
A4: U5.26 (PC3); also elsewhere on the board
CMD_EV1: U5.11 (PD7); also elsewhere on the board
FLOW: U5.2 (PD4); also elsewhere on the board
GND: C5.1, C7.2, C8.1, C9.1, C13.1, D1.1 (K), D3.1 (K), J7.6 (GND), U5.3 (GND), U5.5 (GND), U5.21 (GND), U6.4 (GND), Y1.2; also elsewhere on the board
LVL_HIGH: U5.1 (PD3); also elsewhere on the board
LVL_LOW: U5.32 (PD2); also elsewhere on the board
MISO: J7.1 (MISO), U5.16 (PB4)
MOSI: J7.4 (MOSI), U5.15 (PB3)
unnamed: D1.2 (A), D3.2 (A), R12.2
unnamed: C13.2, U5.20 (AREF)
unnamed: R12.1, U5.12 (PB0)
unnamed: U5.7 (XTAL1/PB6), Y1.3
unnamed: U5.8 (XTAL2/PB7), Y1.1
POW_MES: U5.24 (PC1); also elsewhere on the board
RESET: J7.5 (RST), R26.1, U5.29 (~RESET/PC6)
RX: U5.30 (PD0); also elsewhere on the board
SCK: J7.3 (SCK), U5.17 (PB5)
TEMP: U5.14 (PB2), U6.2 (DATA)
TX: U5.31 (PD1); also elsewhere on the board
TX_EN: U5.10 (PD6); also elsewhere on the board

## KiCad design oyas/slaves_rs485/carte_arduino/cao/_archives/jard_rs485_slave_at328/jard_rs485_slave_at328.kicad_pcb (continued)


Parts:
C1, C4, C10, C11, C12: 1nF; C_0603_1608Metric
C2: 10µF; CP_Elec_5x5.9
C3: 100nF; C_0603_1608Metric
D2: SR560; D_DO-15_P12.70mm_Horizontal
D5: BAV99; SOT-23
D11, D12: SD12_SOD323; D_SOD-323
D15: SM712_SOT23; SOT-23
J1: BUS_IN; TerminalBlock_Phoenix_MPT-0,5-4-2.54_1x04_P2.54mm_Horizontal
J2: BUS_OUT; TerminalBlock_Phoenix_MPT-0,5-4-2.54_1x04_P2.54mm_Horizontal
R1, R2, R3: 100; R_0805_2012Metric_Pad1.20x1.40mm_HandSolder
R4: 40k; R_0805_2012Metric_Pad1.20x1.40mm_HandSolder
R5: 100k; R_0805_2012Metric_Pad1.20x1.40mm_HandSolder
S1: RDS-16S-74385-SMT; BPC_RDS-16S-74385-SMT; PARTREV 1.0
TP1, TP2, TP3, TP4, TP6, TP7, TP8, TP9, TP10: TestPoint; TestPoint_Pad_D1.5mm
U1: BPC_Alim5V
U2: MAX485E; SO-8_3.9x4.9mm_P1.27mm

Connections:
+5V: C1.1, C2.2, C3.1, C4.1, D5.2 (A), D12.2 (A2), TP8.1, U1.7 (OUT+), U1.8 (OUT+), U2.8 (VCC); also elsewhere on the board
A1: S1.1; also elsewhere on the board
A2: S1.2; also elsewhere on the board
A3: S1.4; also elsewhere on the board
A4: S1.8; also elsewhere on the board
BUS_A: D11.2 (A2), D15.2 (A2), J1.2, J2.2, TP6.1, U2.7 (B)
BUS_B: D11.1 (A1), D15.1 (A1), J1.3, J2.3, TP3.1, U2.6 (A)
GND: C1.2, C2.1, C3.2, C4.2, C10.2, C11.2, C12.2, D5.1 (K), D12.1 (A1), D15.3 (common), J1.4, J2.4, R4.1, S1.C_1 (C), S1.C_2 (C), TP10.1, U1.3 (IN-), U1.4 (IN-), U1.5 (OUT-), U1.6 (OUT-), U2.5 (GND); also elsewhere on the board
unnamed: D2.2 (A), J1.1, J2.1, TP2.1
unnamed: C11.1, R1.2, U2.2 (~RE), U2.3 (DE)
unnamed: C12.1, R3.2, U2.4 (DI)
unnamed: R2.2, U2.1 (RO)
POWER_12V: D2.1 (K), R5.2, U1.1 (IN+), U1.2 (IN+); also elsewhere on the board
POW_MES: D5.3 (K), R4.2, R5.1, TP9.1; also elsewhere on the board
RX: C10.1, R2.1, TP1.1; also elsewhere on the board
TX: R3.1, TP7.1; also elsewhere on the board
TX_EN: R1.1, TP4.1; also elsewhere on the board


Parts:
C6: 100nF; C_0603_1608Metric
D6, D7, D8, D10: BAV99; SOT-23
D13: 1N4007G; D_A-405_P5.08mm_Vertical_KathodeUp
J3: Débit; TerminalBlock_Phoenix_MPT-0,5-3-2.54_1x03_P2.54mm_Horizontal
J4: Niveaux; TerminalBlock_Phoenix_MPT-0,5-3-2.54_1x03_P2.54mm_Horizontal
J6: EV1; TerminalBlock_Phoenix_MPT-0,5-2-2.54_1x02_P2.54mm_Horizontal
Q4: BPC_FMMT38C; BPC_SOT-23-3
Q6: P03P4L-04; TO-220-3_Vertical
R7, R8, R9: 100; R_0805_2012Metric_Pad1.20x1.40mm_HandSolder
R13: 220; R_0805_2012Metric_Pad1.20x1.40mm_HandSolder
R15, R17: 100k; R_0805_2012Metric_Pad1.20x1.40mm_HandSolder
TP11, TP12, TP13, TP15: TestPoint; TestPoint_Pad_D1.5mm

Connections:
+5V: D6.2 (A), D7.2 (A), D8.2 (A), D10.2 (A), J3.1; also elsewhere on the board
CMD_EV1: D10.3 (K), R13.1, TP15.1; also elsewhere on the board
FLOW: D8.3 (K), R7.2, TP11.1; also elsewhere on the board
GND: C6.2, D6.1 (K), D7.1 (K), D8.1 (K), D10.1 (K), D13.2 (A), J3.3, J4.3, J6.1, Q4.2 (E), R15.2; also elsewhere on the board
LVL_HIGH: D6.3 (K), R8.2, TP12.1; also elsewhere on the board
LVL_LOW: D7.3 (K), R9.2, TP13.1; also elsewhere on the board
unnamed: D13.1 (K), J6.2, Q6.2 (D)
unnamed: J3.2, R7.1
unnamed: J4.1, R9.1
unnamed: J4.2, R8.1
unnamed: C6.1, Q4.1 (B), R13.2, R15.1
unnamed: Q4.3 (C), Q6.1 (G), R17.2
POWER_12V: Q6.3 (S), R17.1; also elsewhere on the board



Board: 2 copper layers, 80.0 x 30.0 mm, 65 parts (39 on the bottom side), 37 nets.

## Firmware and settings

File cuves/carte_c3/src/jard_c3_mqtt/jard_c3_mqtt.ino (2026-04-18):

/**
 * @file jard_c3_mqtt.ino
 * @brief ESP32-C3 - Gestion d'un noeud WIFI-IO de controle de cuve
 * 
 * NOLOGO - ESP C3 super mini
 * 
 * LED Verte   : Fiwe=ON, Clignote si EV active
 * LED interne : Clignote rapide si activité réseau, éteinte si nada
 * LED Rouge   : Fixe=Pas de Wifi, Rapide=Pas de Mqtt, Lent(2s)=Off
 */

#include <WiFi.h>
#include <EspMQTTClient.h>

#include "timer.h"
#include "analog.hpp"

#include "esp_system.h"
#include "esp_sleep.h"
// #include "esp_task_wdt.h"       // Optionnel si tu veux gérer le WDT proprement

//#define NODE_MAIN
//#define NODE_PAUL
//#define NODE_REDUIT
//#define NODE_BARBEC
#define NODE_ARRIERE
//#define NODE_TERRASSE
//#define NODE_TEST

#define VERSION "V1.0-ESP32C3"

/**
 * Reglages
 */
#define TIME_BEFORE_SLEEP_S   (60*60)
#define TIME_BEFORE_FIRST_S   (3*60)
#define TIME_REPEAT_FIRST_S   (20)
#define TIME_CYCLE_MS         (100)
#define TIMEOUT_COMM_S        (5)
#define SLEEPING_TIME_MIN     (30)

/**
 * Credentials Wifi et MQTT
 */
#define WIFI_ID       "Domotique"
#define WIFI_PWD      "94582604"
#define MQTT_IP       "192.168.3.200"
#define MQTT_LOGIN    "toto"
#define MQTT_PWD      "toto"

/**
 * Brochage ESP32-C3 (EXEMPLES) : A ADAPTER !
 * - Choisis des GPIO dispo sur ta carte C3
 * - Pour l'ADC, il faut un GPIO ADC (ADC1) supporté par ton module
 */
#define PIN_IN_N1       3
#define PIN_IN_N2       4
#define PIN_IN_N3       5
#define PIN_OUT_CMD     10
#define PIN_LED_ROUGE   20
#define PIN_LED_VERTE   21

// ADC: sur ESP32-C3, analogRead() se fait sur un GPIO ADC (ex: GPIO0/1/2/3/4 selon carte)
// Mets ici un GPIO réellement câblé vers ta mesure tension
#define PIN_ANALOG_POW  1

/**
 * Sujets MQTT
 */
#define TOPIC_PREFIX  "/wifiio"
#define TOPIC_CMD     "cmd"
#define TOPIC_DATA    "data"
#define TOPIC_LOG     "log"

bool g_comm_ok=false;
bool g_lvl_1=false;
bool g_lvl_2=false;
bool g_lvl_3=false;
int  g_rssi=0;
bool g_cmd_pump=false;
unsigned long g_tick_s=0;
bool g_flg250ms=false;
bool g_flg500ms=false;
bool g_flg1s=false;
bool g_flg2s=false;
bool g_flgImp500ms=false;
bool g_flgImp1s=false;
bool g_flgImp2s=false;

typedef enum
{
  OTHER,
  NORMAL,
  HARD_WDG,
  SOFT_WDG
} E_BOOT_REASON;

E_BOOT_REASON g_eBootReason;
bool g_boot_event_sent=false;

Analog anVoltage=Analog();

Timer tmrComm((unsigned long)TIMEOUT_COMM_S*1000UL);
Timer tmrBeforeSleep((unsigned long)TIME_BEFORE_SLEEP_S*1000UL);
Timer tmrGotoSleep(5000UL);

Timer tmrCycle((unsigned long)TIME_CYCLE_MS,false);
Timer tmr250ms(250UL,false);

Timer tmrBeforeFirst((unsigned long)TIME_BEFORE_FIRST_S*1000UL);
Timer tmrRepeatFirst((unsigned long)TIME_REPEAT_FIRST_S*1000UL,false);

#ifdef NODE_TEST
  char NAME[]="test";
#endif
#ifdef NODE_MAIN
  char NAME[]="main";
#endif
#ifdef NODE_PAUL
  char NAME[]="paul";
#endif
#ifdef NODE_REDUIT
  char NAME[]="reduit";
#endif
#ifdef NODE_BARBEC
  char NAME[]="barbec";
#endif
#ifdef NODE_ARRIERE
  char NAME[]="arriere";
#endif
#ifdef NODE_TERRASSE
  char NAME[]="terrasse";
#endif



EspMQTTClient mqttClient(
  WIFI_ID,
  WIFI_PWD,
  MQTT_IP,
  MQTT_LOGIN,
  MQTT_PWD,
  NAME
);

void sendLog(const char *strMsg)
{
  char strTopicLog[64];
  snprintf(strTopicLog,sizeof(strTopicLog),"%s/%s/%s",TOPIC_PREFIX,TOPIC_LOG,NAME);
  Serial.print("Log into ");
  Serial.println(strTopicLog);
  mqttClient.publish(strTopicLog, strMsg);
}

void addBool(char *strJson,const char *strKey,bool val)
{
  strcat(strJson,"\"");
  strcat(strJson,strKey);
  strcat(strJson,"\":");
  strcat(strJson, val ? "true" : "false");
}

void addInt(char *strJson,const char *strKey,int val)
{
  strcat(strJson,"\"");
  strcat(strJson,strKey);
  strcat(strJson,"\":");
  char tmp[16];
  snprintf(tmp,sizeof(tmp),"%d",val);
  strcat(strJson,tmp);
}

void addUshort(char *strJson,const char *strKey,unsigned short val)
{
  strcat(strJson,"\"");
  strcat(strJson,strKey);
  strcat(strJson,"\":");
  char tmp[16];
  snprintf(tmp,sizeof(tmp),"%u",val);
  strcat(strJson,tmp);
}

void addULong(char *strJson,const char *strKey,unsigned long val)
{
  strcat(strJson,"\"");
  strcat(strJson,strKey);
  strcat(strJson,"\":");
  char tmp[24];
  snprintf(tmp,sizeof(tmp),"%lu",val);
  strcat(strJson,tmp);
}

void sendData(void)
{
  char strTopicData[64];
  snprintf(strTopicData,sizeof(strTopicData),"%s/%s/%s",TOPIC_PREFIX,TOPIC_DATA,NAME);
  Serial.print("Data to ");
  Serial.println(strTopicData);

  char strData[255]="";
  strcat(strData,"{");
  addBool(strData,"cmd",g_cmd_pump); strcat(strData,",");
  addBool(strData,"n1",g_lvl_1);     strcat(strData,",");
  addBool(strData,"n2",g_lvl_2);     strcat(strData,",");
  addBool(strData,"n3",g_lvl_3);     strcat(strData,",");
  addInt (strData,"rssi",g_rssi);    strcat(strData,",");

  // ⚠️ Calibration ADC différente sur ESP32-C3 !
  // Tu auras probablement besoin d'ajuster cette formule.
  // Ici on garde ton ancien calcul en "placeholder".
  unsigned short dxvolt = (unsigned short)(120UL * anVoltage.get() / 3286UL);
  addUshort(strData,"pwr",dxvolt);   strcat(strData,",");
  addULong(strData,"tick",g_tick_s);
  strcat(strData,"}");

  mqttClient.publish(strTopicData, strData);
}

void onReceiveCmd(const String &payload)
{  
  Serial.print("Cmd: ");
  Serial.println(payload);

  tmrBeforeFirst.stop();
  tmrRepeatFirst.stop();

  if (tmrGotoSleep.isRunning())
  {
    Serial.println("Cmd ignoree car veille demandee.");
    return;
  }

  if (payload=="on")
    g_cmd_pump=true;
  else if (payload=="off")
    g_cmd_pump=false;
  else if (payload=="sleep")
  {
    g_cmd_pump=false;
    sendLog("Demande de faire dodo!");
    tmrGotoSleep.start();
  }
  else if (payload=="ping")
    sendLog("pong");
  else if (payload=="tstwdg")
  {
    while (1) { } // laisser le watchdog faire son boulot
  }
  else if (payload=="tstwdg2")
  {
    // Sur ESP32, désactiver le WDT n'est pas "ESP.wdtDisable()".
    // Si tu en as besoin, on le fera proprement avec esp_task_wdt_*.
    sendLog("tstwdg2 non implemente (ESP32)");
    while (1) { }
  }

  sendData();

  g_comm_ok=true;
  tmrComm.start();
  tmrBeforeSleep.start();
}

void onConnectionEstablished()
{
  char strTopicCmd[64];
  snprintf(strTopicCmd,sizeof(strTopicCmd),"%s/%s/%s",TOPIC_PREFIX,TOPIC_CMD,NAME);
  mqttClient.subscribe(strTopicCmd,onReceiveCmd);

  char strConnMsg[80];
  snprintf(strConnMsg,sizeof(strConnMsg),"Connected %s (%s %s)",VERSION,__DATE__,__TIME__);

  sendLog(strConnMsg);
  sendData();

  if (!g_boot_event_sent)
  {
    switch (g_eBootReason)
    {
      case NORMAL:   break;
      case SOFT_WDG: sendLog("SOFT WDG!"); break;
      case HARD_WDG: sendLog("HARD WDG!"); break;
      case OTHER:    sendLog("OTHER BOOT!"); break;
    }
    g_boot_event_sent=true;
  }
}

void setup_mqtt(void)
{
  static char strName[32];
  snprintf(strName,sizeof(strName),"wifiio_%s",NAME);
  mqttClient.setMqttClientName(strName);

  mqttClient.enableMQTTPersistence();
  mqttClient.enableDebuggingMessages(); // si tu veux tracer
}

inline void _point(void)
{
  digitalWrite(PIN_LED_ROUGE,LOW);
  digitalWrite(LED_BUILTIN,LOW);
  delay(100);
  digitalWrite(PIN_LED_ROUGE,HIGH);
  digitalWrite(LED_BUILTIN,HIGH);
  delay(200);
}

inline void _trait(void)
{
  digitalWrite(PIN_LED_ROUGE,LOW);
  digitalWrite(LED_BUILTIN,LOW);
  delay(400);
  digitalWrite(PIN_LED_ROUGE,HIGH);
  digitalWrite(LED_BUILTIN,HIGH);
  delay(200);
}

inline void _sos(void)
{
  for (int i=0;i<10;i++)
  {
    digitalWrite(PIN_OUT_CMD,LOW);

    for (int j=0;j<3;j++) _point();
    delay(100);

    for (int j=0;j<3;j++) _trait();
    delay(100);

    for (int j=0;j<3;j++) _point();

    delay(1000);
  }
}

static E_BOOT_REASON mapBootReason()
{
  // ESP32: cause de reset
  esp_reset_reason_t r = esp_reset_reason();

  switch (r)
  {
    case ESP_RST_POWERON:
    case ESP_RST_SW:
    case ESP_RST_EXT:
      return NORMAL;

    case ESP_RST_TASK_WDT:
      return SOFT_WDG;

    case ESP_RST_WDT:
    case ESP_RST_PANIC:
      return HARD_WDG;

    default:
      return OTHER;
  }
}

void setup()
{
  pinMode(PIN_OUT_CMD,OUTPUT);
  digitalWrite(PIN_OUT_CMD,LOW);

  pinMode(PIN_LED_ROUGE,OUTPUT);
  digitalWrite(PIN_LED_ROUGE,LOW);

  pinMode(LED_BUILTIN,OUTPUT);
  digitalWrite(LED_BUILTIN,LOW);  

  pinMode(PIN_LED_VERTE,OUTPUT);
  digitalWrite(PIN_LED_VERTE,LOW);

  pinMode(PIN_IN_N1,INPUT_PULLUP);
  pinMode(PIN_IN_N2,INPUT_PULLUP);
  pinMode(PIN_IN_N3,INPUT_PULLUP);

  pinMode(PIN_ANALOG_POW,INPUT);

  Serial.begin(9600);
  delay(300);
  Serial.println("Boot");

  g_eBootReason = mapBootReason();
  g_boot_event_sent = false;

  if ((g_eBootReason==SOFT_WDG) || (g_eBootReason==HARD_WDG))
    _sos();

  setup_mqtt();

  g_comm_ok=false;

  tmrComm.start();
  tmrCycle.start();
  tmrBeforeSleep.start();
  tmrBeforeFirst.start();
  tmrRepeatFirst.start();
  tmr250ms.start();
}

void goDeepSleep()
{
  g_cmd_pump=false;
  digitalWrite(PIN_OUT_CMD,LOW);
  digitalWrite(PIN_LED_ROUGE,LOW);
  digitalWrite(PIN_LED_VERTE,LOW);
  digitalWrite(LED_BUILTIN,HIGH);
  

  // Réveil timer uniquement (simple et fiable)
  uint64_t us = (uint64_t)SLEEPING_TIME_MIN * 60ULL * 1000000ULL;
  esp_sleep_enable_timer_wakeup(us);
  esp_deep_sleep_start();
}

void loop()
{
  // Lecture des niveaux
  g_lvl_1 = (digitalRead(PIN_IN_N1)==LOW);
  g_lvl_2 = (digitalRead(PIN_IN_N2)==LOW);
  g_lvl_3 = (digitalRead(PIN_IN_N3)==LOW);

  // Lecture lente tension + RSSI
  if (tmrCycle.tick())
  {
    unsigned short tmp = (unsigned short)analogRead(PIN_ANALOG_POW);
    anVoltage.latch(tmp);

    g_rssi = WiFi.RSSI();
  }

  // Timeout comm
  if (tmrComm.tick())  
    g_comm_ok=false;

  // Pompe OFF si plus de comm
  if (!g_comm_ok)
    g_cmd_pump=false;

  // Pompe OFF si on va dormir
  if (tmrGotoSleep.isRunning())
    g_cmd_pump=false;

  // MQTT
  mqttClient.loop();

  // Phase post-boot : on renvoie les data en boucle
  if (tmrBeforeFirst.isRunning())
  {
    if (tmrRepeatFirst.tick())
      sendData();
  }

  // Fin du temps post-boot sans commande -> sommeil
  if (tmrBeforeFirst.tick())
  {
    Serial.println("Pas de reponse...");
    sendLog("No answer means sleep...");
    tmrGotoSleep.start();
  }

  // Au bout d'1h sans commande -> demande de sommeil
  if (tmrBeforeSleep.tick())
  {
    Serial.println("Sleep...");
    sendLog("Now time to sleep...");
    tmrGotoSleep.start();
  }

  // Deadline avant sommeil -> deep sleep
  if (tmrGotoSleep.tick())
    goDeepSleep();

  // Tick 250 milli-secondes
  if (tmr250ms.tick())
  {
    g_flgImp500ms=false;
    g_flgImp1s=false;
    g_flgImp2s=false;
    
    g_flg250ms=!g_flg250ms;
    if (g_flg250ms==false)
    {
      g_flgImp500ms=true;
      g_flg500ms=!g_flg500ms;
      if (g_flg500ms==false)
      {
        g_flgImp1s=true;
        g_flg1s=!g_flg1s;
        g_tick_s++;
        if (g_flg1s==false)
        {
          g_flgImp2s=true;
          g_flg2s=!g_flg2s;
        }
      }
    }
  }

  // Application sortie pompe + LED
  if (g_cmd_pump)
  {
    digitalWrite(PIN_OUT_CMD,HIGH);    
    digitalWrite(PIN_LED_VERTE,g_flg500ms==true?HIGH:LOW);
  }
  else
  {
    digitalWrite(PIN_OUT_CMD,LOW);
    digitalWrite(PIN_LED_VERTE,g_comm_ok==true?HIGH:LOW);
  }

  if (g_comm_ok==true)
  {
    digitalWrite(LED_BUILTIN,g_flg500ms==true ? LOW : HIGH);
    digitalWrite(PIN_LED_ROUGE,LOW);    
  }
  else
  {
    digitalWrite(LED_BUILTIN,HIGH);
    
    if (!mqttClient.isWifiConnected())
    {
      digitalWrite(PIN_LED_ROUGE,HIGH);
    }
    else if (!mqttClient.isMqttConnected())
    {
      digitalWrite(PIN_LED_ROUGE,g_flg250ms==true ? HIGH : LOW);
    }
    else
    {
      digitalWrite(PIN_LED_ROUGE,g_flgImp2s==true ? HIGH : LOW);
    }
  }
}

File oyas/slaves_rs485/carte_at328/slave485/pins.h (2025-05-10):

#ifndef PINS_HEADER_INCLUDED
#define PINS_HEADER_INCLUDED

#define PIN_CPT_LVL_LOW			(9)
#define PIN_CPT_LVL_HIGH		(10)
#define PIN_CPT_FLOW			(8)
#define PIN_TX_EN				(A5)
#define PIN_CMD_EV				(7)
#define PIN_LED					(18)

#define PIN_MES_V				(A2)
#define PIN_ADDR_A1				(3)
#define PIN_ADDR_A2				(6)
#define PIN_ADDR_A3				(4)
#define PIN_ADDR_A4				(5)

#define PIN_DGB_SYNC			(A0)      ///< @remark A 1 pendant les mesures (temp/hum)
#define PIN_DGB_CMD				(12)      ///< @remark Change d'etat à chaque reception de commande

#endif

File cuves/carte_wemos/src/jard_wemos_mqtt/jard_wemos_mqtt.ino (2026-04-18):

/**
 * @file jard_wemos_mqtt.ino
 * @brief PROGRAMME PRINCIPAL - Gestion d'un noeud WIFI-IO de controle de cuve
 * 
 * @warning Connecter D0 (GPIO16) a RST et mettre D0 en entree sans pullup
*/
#include <ESP8266WiFi.h>
#include <EspMQTTClient.h>

#include "timer.h"
#include "analog.hpp"

//#define NODE_MAIN
//#define NODE_PAUL
//#define NODE_REDUIT
//#define NODE_BARBEC
//#define NODE_ARRIERE
#define NODE_TERRASSE
//#define NODE_TEST

#define VERSION "V1.0"

/**
 * @brief Reglages
 * @{
*/
#define TIME_BEFORE_SLEEP_S   (60*60)   ///< Temps au bout duquel on va en veille quand on ne recoit plus de commandes
#define TIME_BEFORE_FIRST_S   (3*60)    ///< Temps laisse au serveur pour repondre avant de partir en veille (apres un boot)
#define TIME_REPEAT_FIRST_S   (20)      ///< Frequence de repetition des envois de data (apres un boot)
#define TIME_CYCLE_MS         (100)     ///< Temps de cycle
#define TIMEOUT_COMM_S        (5)       ///< Temps au bout duquel on considere la comm KO (provoque la coupure de la pompe)
#define SLEEPING_TIME_MIN     (30)      ///< Temps de veille du micro avant de re-donner des nouvelles au reseau 
/**
 * @}
*/

/**
 * @brief Credentials Wifi et MQTT
 * @{
*/
#define WIFI_ID       "Domotique"
#define WIFI_PWD      "94582604"
#define MQTT_IP       "192.168.3.200"
#define MQTT_LOGIN    "toto"
#define MQTT_PWD      "toto"
/**
 * @}
*/

/**
 * @brief Brochage du micro
 * @{
*/
#define PIN_IN_N1       14
#define PIN_IN_N2       12
#define PIN_IN_N3       13
#define PIN_OUT_CMD     15
#define PIN_LED         2
#define PIN_ANALOG_POW  A0
#define PIN_WAKEUP      16    ///< (D0 du weemos)
/**
 * @}
*/

//#define MQTT_TRACE_ON

/**
 * @brief Sujets MQTT
 * @{
*/
#define TOPIC_PREFIX  "/wifiio"
#define TOPIC_CMD     "cmd"
#define TOPIC_DATA    "data"
#define TOPIC_LOG     "log"
/**
 * @}
*/

bool g_comm_ok=false;
bool g_lvl_1=false;
bool g_lvl_2=false;
bool g_lvl_3=false;
int g_rssi=0;
bool g_cmd_pump=false;
unsigned long g_tick_s=0;

typedef enum
{
  OTHER,
  NORMAL,
  HARD_WDG,
  SOFT_WDG
} E_BOOT_REASON;

E_BOOT_REASON g_eBootReason;
bool g_boot_event_sent=false;

Analog anVoltage=Analog();

Timer tmrComm((unsigned long)TIMEOUT_COMM_S*1000UL,false);
Timer tmrCycle((unsigned long)TIME_CYCLE_MS,false);
Timer tmrBeforeSleep((unsigned long)TIME_BEFORE_SLEEP_S*1000UL);
Timer tmrGotoSleep(5000UL);
Timer tmrTick1S(1000UL,false);

Timer tmrBeforeFirst((unsigned long)TIME_BEFORE_FIRST_S*1000UL);
Timer tmrRepeatFirst((unsigned long)TIME_REPEAT_FIRST_S*1000UL,false);

#ifdef NODE_TEST
  char NAME[]="test";
#endif
#ifdef NODE_MAIN
  char NAME[]="main";
#endif
#ifdef NODE_PAUL
  char NAME[]="paul";
#endif
#ifdef NODE_REDUIT
  char NAME[]="reduit";
#endif
#ifdef NODE_BARBEC
  char NAME[]="barbec";
#endif
#ifdef NODE_ARRIERE
  char NAME[]="arriere";
#endif
#ifdef NODE_TERRASSE
  char NAME[]="terrasse";
#endif


/**
 * @brief Instance du client MQTT qui va gerer le bordel
*/
EspMQTTClient mqttClient(
  WIFI_ID,    ///< ID Wifi
  WIFI_PWD,   ///< Mot de passe Wifi
  MQTT_IP,    ///< Adresse IP du broker de message
  MQTT_LOGIN, ///< Login MQTT
  MQTT_PWD,   ///< Mot de passe MQTT
  NAME        ///< Nom du noeud (ID MQTT - @warning Doit etre unique et associe au noeud)
);

/**
 * @brief Envoi d'un log MQTT
 * @param[in] Message a logguer
*/
void sendLog(char *strMsg)
{
  char strTopicLog[50];
  sprintf(strTopicLog,"%s/%s/%s",TOPIC_PREFIX,TOPIC_LOG,NAME);
  Serial.print("Log into ");
  Serial.println(strTopicLog);
  mqttClient.publish(strTopicLog, strMsg);
}

/**
 * @brief Ajout d'un Bool au texte JSON donne
 * @param[in,out] strJson Texte JSON en cours (on y ajoute le champ)
 * @param[in] strKey Nom du champ
 * @param[in] val Valeur du champ
*/
void addBool(char *strJson,const char *strKey,bool val)
{
  strcat(strJson,"\"");
  strcat(strJson,strKey);
  strcat(strJson,"\":");
  if (val==true)
    strcat(strJson,"true");
  else
    strcat(strJson,"false");  
}

/**
 * @brief Ajout d'un Int au texte JSON donne
 * @param[in,out] strJson Texte JSON en cours (on y ajoute le champ)
 * @param[in] strKey Nom du champ
 * @param[in] val Valeur du champ
*/
void addInt(char *strJson,const char *strKey,int val)
{
  strcat(strJson,"\"");
  strcat(strJson,strKey);
  strcat(strJson,"\":");
  char tmp[15];
  sprintf(tmp,"%d",val);
  strcat(strJson,tmp);
}

/**
 * @brief Ajout d'un UShort au texte JSON donne
 * @param[in,out] strJson Texte JSON en cours (on y ajoute le champ)
 * @param[in] strKey Nom du champ
 * @param[in] val Valeur du champ
*/
void addUshort(char *strJson,const char *strKey,unsigned short val)
{
  strcat(strJson,"\"");
  strcat(strJson,strKey);
  strcat(strJson,"\":");
  char tmp[15];
  sprintf(tmp,"%d",val);
  strcat(strJson,tmp);
}

/**
 * @brief Ajout d'un ULong au texte JSON donne
 * @param[in,out] strJson Texte JSON en cours (on y ajoute le champ)
 * @param[in] strKey Nom du champ
 * @param[in] val Valeur du champ
*/
void addULong(char *strJson,const char *strKey,unsigned long val)
{
  strcat(strJson,"\"");
  strcat(strJson,strKey);
  strcat(strJson,"\":");
  char tmp[20];
  sprintf(tmp,"%ld",val);
  strcat(strJson,tmp);
}

/**
 * @brief Envoi de la donnee relative au noeud dans le topic associe
*/
void sendData(void)
{
  char strTopicLog[50];
  sprintf(strTopicLog,"%s/%s/%s",TOPIC_PREFIX,TOPIC_DATA,NAME);
  Serial.print("Data to ");
  Serial.println(strTopicLog);

  char strData[255]="";
  strcat(strData,"{");
  addBool(strData,"cmd",g_cmd_pump);
  strcat(strData,",");
  addBool(strData,"n1",g_lvl_1);
  strcat(strData,",");
  addBool(strData,"n2",g_lvl_2);
  strcat(strData,",");
  addBool(strData,"n3",g_lvl_3);
  strcat(strData,",");
  addInt(strData,"rssi",g_rssi);
  strcat(strData,",");
  unsigned short dxvolt=120*anVoltage.get()/939;
  addUshort(strData,"pwr",dxvolt);
  strcat(strData,",");
  addULong(strData,"tick",g_tick_s);
  strcat(strData,"}");
  
  mqttClient.publish(strTopicLog, strData);
}
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

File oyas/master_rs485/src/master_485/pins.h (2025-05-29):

/**
 * @file pins.h
 *
 * @brief Definition des broches de la carte Master RS485
 *
 * Serial2: Wifi
 * Serial3: Log
**/
#ifndef PINS_HEADER_INCLUDED
#define PINS_HEADER_INCLUDED

#define PIN_TX_EN         (6)     ///< Activation de la ligne RS485 (Pour emettre)
#define PIN_TEST_BTN      (2)     ///< Bouton de test (pull up interne)
#define PIN_PWR_ON        (8)     ///< Commande puissance sur réseau RS485 (esclaves)
#define PIN_DATA_LEDS     (4)     ///< Commande Data des LEDs
#define PIN_PWR_LEDS_INV  (5)     ///< Alimentation des LEDs (via pnp / Carte RevA)
#define PIN_PWR_WIFI_INV  (7)     ///< Alimentation module wifi (via pnp / Carte RevA)
#define PIN_PWR_LEDS      (9)     ///< Alimentation des LEDs (via npn)
#define PIN_PWR_WIFI      (10)    ///< Alimentation module wifi (via npn)


#endif

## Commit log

2024-08-23 Import sources du maitres 485 à partir du repo d'origine (module_uino)
    [board_rs485_master.kicad_pcb, board_rs485_master.kicad_sch, board_rs485_master.xlsx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]
2024-08-23 Deplacement carte maitre rs485
    [board_rs485_master.kicad_pcb, board_rs485_master.kicad_sch, board_rs485_master.xlsx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]
2024-08-23 Import du projet esclave
    [ES.kicad_sch, jard_rs485_slave_at328.kicad_pcb, jard_rs485_slave_at328.kicad_sch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]
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2024-08-24 Ajout carte weemos_mqtt et sources
    [jard_wemos.kicad_pcb, jard_wemos.kicad_sch]
2024-08-24 Logiciel de commande des cuves (Client PC Windows) Design des filtres (meca)
    [Ecrou_filetageARevoir.FCStd, bouchon_filtrant.FCStd, bouchon_pressostat.FCStd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]
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2024-08-24 Import carte Jarduino2 du repo
    [jarduino2.kicad_pcb, jarduino2.sch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]
2024-09-28 Import du code de la Gateway Domotique (Tel qu'utilisé été 2024)
    [2023-07-18_to_08-05_datas.csv]
2025-02-16 Commentaires todo
    [jard_rs485_slave_mods2.kicad_sch]
2025-03-01 Creation carte oya à base de MSP430
    [jard_rs485_slave_msp430.kicad_pcb, jard_rs485_slave_msp430.kicad_sch]
2025-03-02 Réarragement du dossier
    [ES.kicad_sch, jard_rs485_slave_at328.kicad_pcb, jard_rs485_slave_at328.kicad_sch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]
2025-03-02 Creation carte esclave à base de AT328 (à finir - Connecter power 12V mes, ...)
    [jard_rs485_slave_at328.kicad_pcb, jard_rs485_slave_at328.kicad_sch]
2025-03-02 Correction valeurs des capas du quartz
    [jard_rs485_slave_msp430.kicad_sch]
2025-03-02 Finalisation carte AT328
    [jard_rs485_slave_at328.kicad_pcb, jard_rs485_slave_at328.kicad_sch]
2025-03-02 Renommage jard_wemos
    [jard_wemos.kicad_pcb, jard_wemos.kicad_sch]
2025-04-12 Corrections sur la carte Rev A MSP430
    - Pas de pullup interne ds MSP430
    - Correction sérigraphie et empreinte connecteur de PROG
    - Décalage LED
    - Suppression de l'entrée débit
    - Empreinte des doides TVS et des capas pour être soudables à la main
    - Empreinte D12 horizontale
    - C8 et C10 en 805 au lieu de 603
    - Grossissement de la sérigraphie de version
    [jard_rs485_slave_msp430.kicad_pcb, jard_rs485_slave_msp430.kicad_sch]
2025-04-12 Suite fabrication 2025 (ajout d'info)
    [nomenclature.xlsx]
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2025-04-13 Vérification du nouveau design (Rev B)
    [jard_rs485_slave_msp430.kicad_pcb, jard_rs485_slave_msp430.kicad_sch]
2025-04-15 Finitions + Revérification
    [jard_rs485_slave_msp430.kicad_pcb, jard_rs485_slave_msp430.kicad_sch]
2025-04-15 Empreinte TVS
    [jard_rs485_slave_msp430.kicad_pcb, jard_rs485_slave_msp430.kicad_sch]
2025-04-16 Finalisation et test des règles
    [jard_c3.kicad_pcb, jard_c3.kicad_sch]
2025-04-18 Améliorations sur carte AT328
    - Capas en hand soldering et en 805
    - TP + gros
    - Repères composants
    - Carte moins longue
    [jard_rs485_slave_at328.kicad_pcb, jard_rs485_slave_at328.kicad_sch]
2025-05-08 Modification valeurs de composants - C10 100nF - R4 25k - C12 1µF
    [jard_rs485_slave_msp430.kicad_sch]
2025-05-08 Déplacement du projet de carte MSP430
    [jard_rs485_slave_msp430.kicad_pcb, jard_rs485_slave_msp430.kicad_sch]
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2025-05-08 Déplacement des projets hard: Modules arduino et carte at328
    [ES.kicad_sch, jard_rs485_slave_at328.kicad_pcb, jard_rs485_slave_at328.kicad_sch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]
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2025-05-08 Annotation erreurs
    [jard_c3.kicad_sch]
2025-05-08 Réamménagement des projets de cartes pour les cuves
    [jard_c3.kicad_pcb, jard_c3.kicad_sch, jard_wemos.kicad_pcb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]
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2025-05-14 Test d'aujourd'hui. Quelques soudures mal faites... + Reset non fonctionnel => Mettre 100nF ? (Ou bien quartz nok / capas ?)
    [main.c]
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2025-05-26 Modif MAX485 -> MAX3485 (3.3V)
    [jard_rs485_slave_msp430.kicad_sch]
2025-05-28 MAJ correction limitation du courant de base des pnp (Pwr Wifi et LEDs)
    [board_rs485_master.kicad_pcb, board_rs485_master.kicad_sch, bus.kicad_sch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]
2025-05-29 Ajout de la nouvelle configuration du maître des Oyas (Paul / C) Déclenchement tous les jours à midi +Corr.Bugs
    [jard_rs485_master.ino, pins.h, wificomm.cpp]
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2025-06-15 Idées version suivante
    [board_rs485_master.kicad_sch]
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2025-11-25 Creation CAO de la carte testeur d'OYA
    On branche le tester en un point du réseau.
    On configure l'adresse à piloter à l'aide d'un bouton + 7 SEG
    On actionne ON/OFF avec un autre bouton
    [oya_tester.kicad_pcb, oya_tester.kicad_sch]
2025-12-12 Changement forme de la carte (boîte de dérivation)
    [oya_tester.kicad_pcb, oya_tester.kicad_sch]
2025-12-12 Finalisation testeur Connecteurs des interrupteurs à choisir...
    [oya_tester.kicad_pcb, oya_tester.kicad_sch]
2026-01-16 Réception rev A et corrections: - Les SW étaient à 5V au lieu de GND - Idem sur le connecteur JST du SW ON/OFF - Valeur des résistances anodes du 7seg à 220 Ohms
    Passage en Rev B pour la suivante
    + Ajout su soft de départ
    [oya_tester.kicad_pcb, oya_tester.kicad_sch]
2026-02-18 Création d'une carte oya avec M0
    - Plus perenne que MSP430F1232
    - Pas besoin de quartz/resonateur externe
    - Compatible avec la sonde AVR ATMEGA
    - Possibilité d'une config de mesure du débit
    [alim_es.kicad_sch, jard_rs485_slave_m0.kicad_pcb, jard_rs485_slave_m0.kicad_sch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]
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2026-03-06 Revue de carte et de routage:
    - Amélioration découplage micro (1uF 805 sur VDDCore et 100nF 603 sur les autres selon recommendation microchip)
    - R14=1k: Moins de courant dans Q1
    - R1=R2=1k: Limiter le clamp en mode débit
    - R3 NM en mode débit
    - C17=100nF pour améliorer filtrage 3.3V
    - Ajout Capa 100nF sur reset
    [alim_es.kicad_sch, jard_rs485_slave_m0.kicad_pcb, micro.kicad_sch]
2026-03-07 Fin de revue avec ajout d'une diode TVS 18V en entrée
    [alim_es.kicad_sch, jard_rs485_slave_m0.kicad_pcb, jard_rs485_slave_m0.kicad_sch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]
2026-03-11 Quelques commentaires sur le schéma pour préparer la version 2027...
    [bus.kicad_sch, cpu.kicad_sch, power.kicad_sch]
2026-03-11 Correction de la capacité de la cuve
2026-03-14 Changement de la forme de la carte: Boîte 85 x 85 x 55
    [jard_c3.kicad_pcb, jard_c3.kicad_sch]
2026-03-14 Finalisation / règles kicad...
    [jard_c3.kicad_pcb, jard_c3.kicad_sch]
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2026-04-13 Préparation future carte Rev B (Inversion TX/RX) Programme en cours de test
    [alim_es.kicad_sch, jard_rs485_slave_m0.kicad_pcb, jard_rs485_slave_m0.kicad_sch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]
2026-04-15 Amélioration pad de R10 Sortie du module adc Calibration de la mesure d'alim
    [jard_rs485_slave_m0.kicad_pcb]
2026-04-17 Changement connecteur de programmation
    [jard_rs485_slave_m0.kicad_pcb, micro.kicad_sch]
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2026-04-26 Préparation carte future Rev B (Correction SW) Mise au point programme.
    [oya_tester.kicad_sch]
2026-05-13 Ajout des voyants
    Rouge lent: Veille
    Rouge rapide: Off
    Rouge très rapide: Booting...
    Rouge Fixe + Bleu Lent: On
    Rouge Fixe + Bleu Rapide: Au moins une pompe en route
    [jard_voyants.py, jard_wemos_mqtt_mgr.py, test_voyants.py]
2026-05-13 Finalisation future Rev B
    Ajout de protections sur le 12V Bus
    [oya_tester.kicad_pcb, oya_tester.kicad_sch]
2026-05-13 Finalisation Future Rev B
    [alim_es.kicad_sch, jard_rs485_slave_m0.kicad_pcb, jard_rs485_slave_m0.kicad_sch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]
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2026-05-15 Nouveau code voyants:
    -Rouge 250ms: Erreur (service down...)
    -Rouge 2S: Veille
    -Rouge 1S: Off
    -Rouge Fixe - Bleu 2S: Réveil en cours (au moins 1 module en sleep)
    -Rouge fixe - Bleu 1S: ON
    -Rouge fixe - Bleu 250ms: Au moins une pompe active
    [jard_voyants.py]
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2026-05-24 Gestion remplissage au niveau + correction bug (le retour ack provoque data à 0) Weemos: Meilleur timeout de sleep
    [jardWS.py, jard_oyas_client.py, jard_oyas_mqtt_mgr.py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]
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2026-06-01 Debug champ rmt: Bug dans firmware (cf état wifi remote = Pas de latch des datas) Gestion on/off par module en + du on/off application Codage fonction de réparation/nettoyage EV (à tester)
    [jardWS.py, jard_oyas_client.py, jard_oyas_mqtt_mgr.py]
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
